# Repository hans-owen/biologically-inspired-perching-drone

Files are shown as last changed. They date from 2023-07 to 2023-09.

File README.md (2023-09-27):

# Biologically Inspired Perching Drone
This project aims to develop an effective attachable modular device for enabling drones to perch on cyclindrical objects, while maintaining the ability to land on flat surfaces. It was originally inspired by the claws of birds of prey and their unique biological ratcheting mechanism that allows them to tightly and securely grip with their talons without relying entirely on muscular strength.

By using 3D printing manufacturing and easy to find off-the-shelf parts we hope to provide a design that is accessible and easily implemented into different drones. Additionally, we hope to make it easy for others to contribute their ideas, modifications, and remixes of original designs.

Currently, only a single preliminary version has been released, which offers effective perching for 5-inch drones that can be manually triggered by a pilot via BetaFlight firmware. Although this is a good first-step/proof-of-concept, the idea has far more potential. Further iterations could offer support to more drones of different sizes and software that functions together with autopilot firmware (e.g., Ardupilot) would allow for full automation.

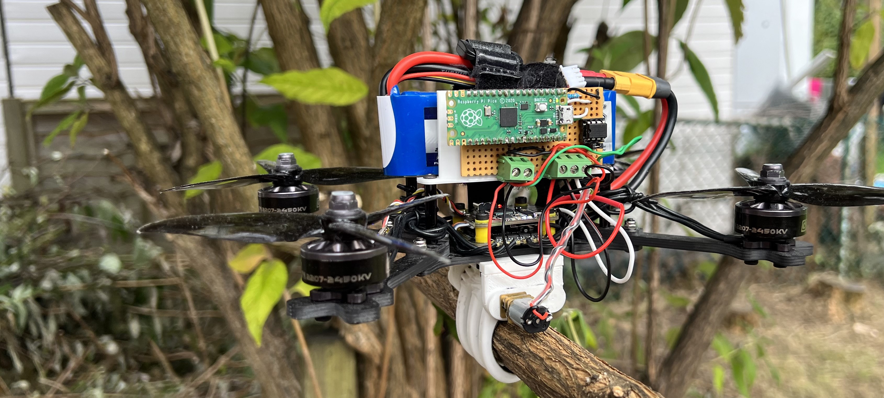
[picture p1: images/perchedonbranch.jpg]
PerchedImage


## Table of Contents
1. Directory Structure
2. Getting Started
   1. 3D Printing
   2. Hardware Assembly
   3. Electronics Assembly
   4. Software
4. How to Use
   1. Setting Up FC firmware
   2. Connect ELRS controller
   3. Actuate Switch
6. Credits
7. Licences

The files within the project contain both the hardware and software required to build a claw attachment for a drone.

## Directory Structure
* [control_code/](./biologically-inspired-perching-drone/claw_control)  - folder containing pico firmware
  * [include/](./biologically-inspired-perching-drone/claw_control/include)
  * [lib/](./biologically-inspired-perching-drone/claw_control/lib)
  * [src/](./biologically-inspired-perching-drone/claw_control/src)
  * [test/](./biologically-inspired-perching-drone/claw_control/test)
  * [platformio.ini](./biologically-inspired-perching-drone/claw_control/platformio.ini)
* [hardware/](./biologically-inspired-perching-drone/hardware)          - folder containing hardware (both electronics & CAD)
* [README.md](./biologically-inspired-perching-drone/README.md)

## Getting Started
To get started with constructing the modular perching attachment for drones ensure you have the following components, links (UK purchasers) have been provided to the exact components used in our version of the build:
#### Claw
* [3D Printer](https://www.crealityofficial.co.uk/products/official-creality-ender-3-3d-printer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)
* [PLA Filament](https://www.amazon.co.uk/s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)
* [4x OD12mm, ID8mm Bearings](https://simplybearings.co.uk/shop/p2772/Budget-MR1282Z-Metal-Shielded-Deep-Groove-Ball-Bearing-8x12x3.5mm/product_info.html)
* [4x 25mm M3 Screws](https://www.accu.co.uk/cap-head-screws/2804-SSC-M3-25-A2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)
* [2x M1.5 Self-tapping Screws](https://cpc.farnell.com/neutrik/a-screw-1-8/screws-for-d-mounts-a-type/dp/AV18050?mckv=s_dc|pcrid|426684131039|kword||match||plid||slid||product|AV18050|pgrid|100371158878|ptaid|pla-1869734976461|&CMP=KNC-GUK-CPC-SHOPPING-9262013734-100371158878-AV18050&s_kwcid=AL!5616!3!426684131039!!!network}!1869734976461!&gclid=CjwKCAjwivemBhBhEiwAJxNWN8YT4Eb2GvifQI9ZS6wh_OzB7m4AdSvY-hiyPY48TIBvsaB6Vbc0dBoCt_0QAvD_BwE)
* [Sand Paper 120 Grit (lower grit works better)](https://www.amazon.co.uk/s?k=sandpaper&crid=HUOTKIT8XZ5P&sprefix=sandpap%2Caps%2C128&ref=nb_sb_noss_2)
* [Super Glue](https://www.amazon.co.uk/Gorilla-4044205-Superglue-15g/dp/B003CT4XT0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)
* [Raspberry Pi Pico](https://thepihut.com/products/raspberry-pi-pico)
* [Metal-Geared DC Motor 298:1](https://thepihut.com/products/micro-metal-gearmotor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)
* [22AWG Black, Red, and White Wire](https://www.amazon.co.uk/TUOFENG-Electric-Flexible-Different-Electronic/dp/B07G72DRKC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)
* [L9110H H-Bridge](https://thepihut.com/products/l9110h-h-bridge-motor-driver-for-dc-motors-8-dip?variant=39823794634947)
* [10Ω Resistor](https://thepihut.com/products/resistor-packs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)
* [Strip Board](https://thepihut.com/products/universal-proto-board-pcbs-4cm-x-6cm-3-pack)

#### Drone
Here is a list of the components we used in the construction of test drone in case you would like directly replicate the build, however this project can be easily adapted to any drone flight controller:
* [SpeedyBee F405V3 Flight Controller + ESC Stack](https://www.unmannedtechshop.co.uk/product/speedybee-f405-v3-bls-50a-4in1-flight-stack/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)
* [Motors](https://cheapdrone.co.uk/dys-sun-fun-sf2207-2207-2400kv-2750kv-4-5s-brushless-motor-cw-thread-for-rc-drone-fpv-racing-drone-parts)
* [BetaFlight ELRS Reciever](https://www.unmannedtechshop.co.uk/product/betafpv-elrs-lite-receiver-2-4ghz-flat-antenna/)
* [TBS Open Source Drone Frame](https://www.quadcopters.co.uk/tbs-source-one/tbs-source-two-racing-frame-v01)
* [LiPo](https://www.amazon.co.uk/GOLDBAT-Battery-Airplane-Quadcopter-Helicopter/dp/B0BVZDYGQ8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)

### 3D Printing
To 3D print the mechanicals parts for the perching claw, you need to download the relevant STL files from the link below:

When printing components with gears ensure that the layers of the print are parallel to the direction of force transmission from the gear to reduce the risk of gears shearing (see below). The design is fully finctional with 100% in-fill PLA, however, can be made more robust using PETG or ABS filaments.

If you wish to remix the hardware designs, the SolidPart files can also be found from the link above and consider submitting the modified design as a remix so that others can easily find custom designs that may be useful for them.

### Hardware Assembly
1. After printing cut out and attach sandpaper to the inside of the claw with superglue to provide a high friction surface for the gripper.
2. Attach the metal-geared DC motor to the side mount of your choice and screw in place with the 1.5mm self tapping screws.
3. After the motor is attached, press-fit the bearings into each of the cut-outs in the side mounts.
4. Press fit the claw onto the motor and bearings, ensure that when the two claw part gears mesh that the claws themselves are parallel with each other.
5. Press fit M3 nuts into the cut-outs on the top mount.
6. Attach and super-glue the top mount to the side mounts with claws attached by inserting the side mount tabs into the top mount.
7. Attach the gripper to the drone by threading the 25mm M3 screws through the flight controller mount and the drone frame, screw them into the nuts of 3D-printed top mount until the FC and the gripper are firmly attached to the drone frame. (Do not overtighten as this can cause damage to your FC!)

This concludes the hardware assembly of this project, next we move onto the electronics and finally conclude with the software.

### Electronics Assembly
We recommend to first layout the circuit on a breadboard (see picture below) and perform a test to ensure all your components are functional before soldering them to a prototyping board.
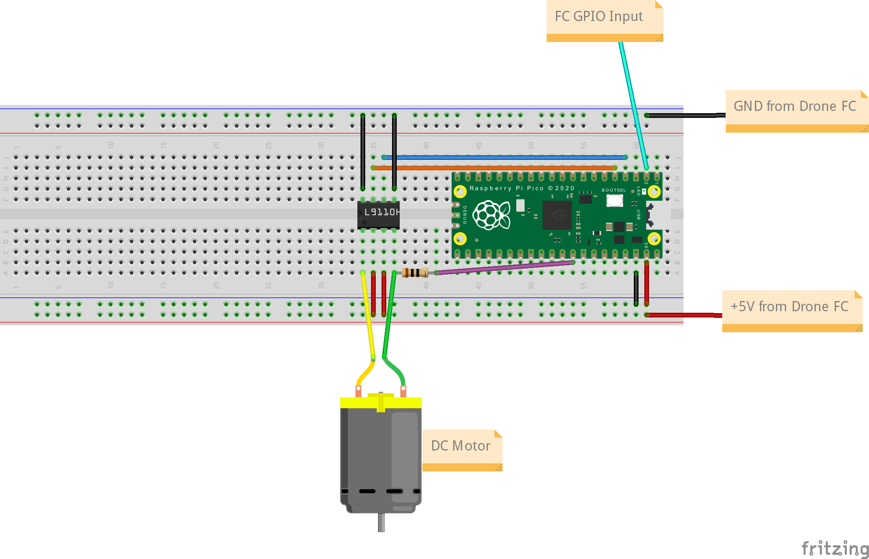
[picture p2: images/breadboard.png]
Breadboard/


The simple circuit uses a Raspberry Pi Pico to take a 3.3V GPIO output from the drone FC and use it to actuate the claw mechanism via an H-bridge. This FC GPIO pin can be mapped to the RF transmitter to manually actuate the claw or be addressed directly in the FC firmware. A shunt resistor is used to measure the current used by the motor and turn off the motor when the claw is fully opened to prevent the mechanism from damaging itself and wasting power. Once the circuit is functional on a breadboard it can easily be soldered together using strip-board for a permanent solution capable of being mounted on the drone.
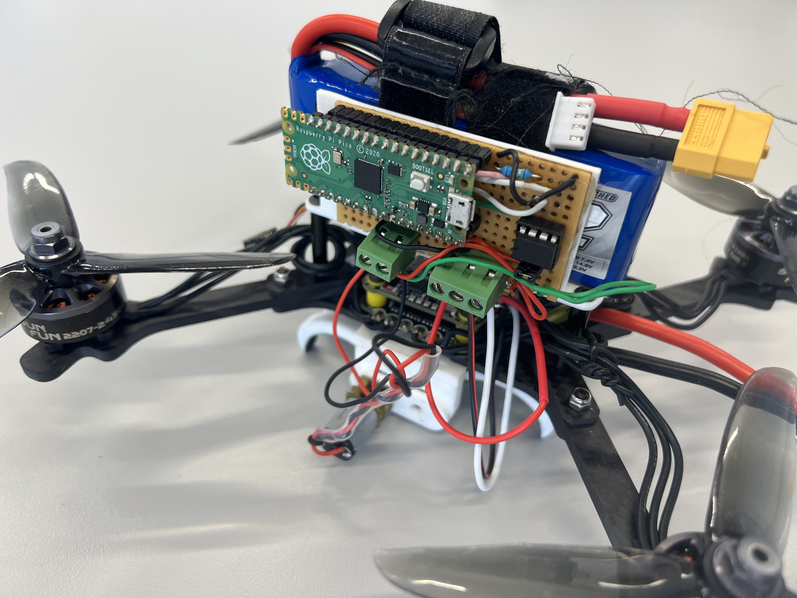
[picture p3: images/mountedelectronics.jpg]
ElectronicsMount/


### Software

The software was developed using VS Code and platform.io to compile the code for the Raspberry Pi Pico using the Arduino framework. To compile the firmware for yourself, download the control_code directory and open in VS Code with the platform.io plug-in, once the project is recognised simply compile the code using platform.io and upload the firmware.uf2 file to the RPi Pico via the boot button. To set up the drone FC firmware see how to use section below.

## How to Use

Once the hardware and electronics have been assembled and the mechanism software has been uploaded, to function the mechanism expects a GPIO output from the FC to actuate the claw. This tutorial focuses on manual actuation of the claw via an RF transmitter used to fly the drone manually, specifically using BetaFlight firmware.

### Setting Up FC Firmware
BetaFlight is the most common drone FC firmware for FPV drones and offers a stable platform for quickly enabling the manual flight of a custom built drone.
1. First set up BetaFlight according to the specifications of your FC of choice and drone set up (link to [General BetaFlight Tutorial](https://www.youtube.com/watch?v=udOHBCORSrE)).
2. To enable a GPIO pin on the FC for the claw mechanism GPIO resource remapping is required, here we have embedded a good YT tutorial with resources that show how to easily implement this with your drone set up. [BetaFlight Resource Remapping Tutorial](https://www.youtube.com/watch?v=-DiGLYbl1Jk).
3. Ensure that the GPIO pad you select on the FC has a wire connecting it to the correct pin on the RPi Pico, along with VCC and GND for powering the Pico.

Another common FC firmware is iNav, which offers some automation advantages over BetaFlight by including automated drone pathing, auto-hover, return-home, etc.
1. Set up iNav according to the specification on your FC and drone set up (link to [General iNav Tutorial](https://www.youtube.com/watch?v=TXAzmrhjKNI)).
2. To perform resource remapping on iNav is more difficult than in BetaFlight, to do this you have to download the [iNav source code](https://github.com/iNavFlight/inav) (relevant version!!), modify the resources in the code and then recompile the firmware and manually upload the firmware to the FC (link to [tutorial](https://www.wizzx.tech/552/)).

### Connecting ELRS Controller
Once the GPIO resource has been effectively remapped according to the firmware type and tutorials above, the controller can be bound to actuate this GPIO pad in the firmware configuration (both BetaFlight and iNav). To do this most often the GPIO resource is mapped to USER1, a custom user selectable mode, when setting up RF transmitter. By setting a switch (AUX1,2,3,4 etc.) on the controller to trigger USER1, it triggers the mechanical claw activation. Reflash firmware after ensuring the controller activates USER1.

### Actuate Switch
Finally, when ready to test, unplug the drone from the firmware configurator and ensure LiPo is plugged in and controller is connected. The claw acutation should now be possible when you activate the switch (AUX1,2,3,4 etc.) on your controller that you mapped to your custom user mode (USER1), which pulls the remapped GPIO pin high for the RPi Pico.

## Credits
[MGCorbin](https://github.com/MGCorbin)
[christiankuhlmann](https://github.com/christiankuhlmann)
[T-Omole](https://github.com/T-Omole)
[hans-owen](https://github.com/hans-owen)

## Licenses
Hardware (all files stored under the [hardware](./biologically-inspired-perching-drone/hardware) folder) are under the Creative Commons Attribution-ShareAlike 4.0 International license.

Firmware (all files stored under the [claw_control](./biologically-inspired-perching-drone/claw_control) folder) are under the MIT license.

See each folders LICENSE.txt file for details.

## Hardware
In this folder you can find STL files that can be downloaded for 3D printing and the original parameterised SolidWorks CAD files and assemblies that can be modified to customise/remix the design to suit different drone and hardware configurations. 
* [Bivalve_7_talon/](./biologically-inspired-perching-drone/hardware/Bivalve_7_talon) - folder containing the Solidworks part files and STL files for a version of the bivalve claw mechanism with additional claws (3-4 config).
* [Bivalve_Claw_Mechanism/](./biologically-inspired-perching-drone/hardware/Bivalve_Claw_Mechanism) - folder containing the SolidWorks part files, STL files, and assembly for the bivalve claw mechanism design.
* [Tendon_Arm/](./biologically-inspired-perching-drone/hardware/Tendon_Arm) - folder contianing the STL files used during the testing and development of the tendon claw design.

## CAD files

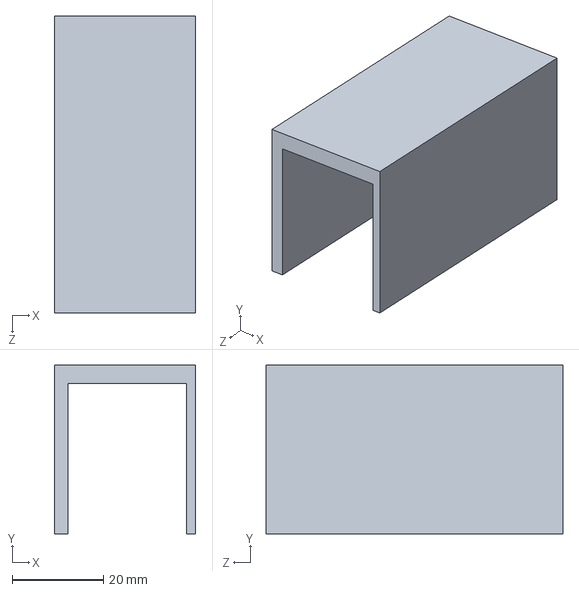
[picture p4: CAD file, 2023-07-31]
hardware/ElectronicsMount.SLDPRT
31.0 x 37.0 x 65.2 mm

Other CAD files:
hardware/ElectronicsMount.STL

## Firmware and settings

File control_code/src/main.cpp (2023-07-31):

#include <Arduino.h>

#define LED_PIN 25
#define FC_SIGNAL_PIN 1
#define MOTOR_FORWARD 2
#define MOTOR_REVERSE 3
#define ADC_PIN 27

int speed = 255;
int currentThreshold = 40;
bool closed = false;

// put function declarations here:
void motorforward() {
  analogWrite(MOTOR_FORWARD, speed);
  analogWrite(MOTOR_REVERSE, 0);
}

void motorreverse() {
  analogWrite(MOTOR_FORWARD, 0);
  analogWrite(MOTOR_REVERSE, speed);
}

void motorstop() {
  analogWrite(MOTOR_FORWARD, 0);
  analogWrite(MOTOR_REVERSE, 0);
}

void showmecurrent() {
  int current = analogRead(ADC_PIN);
  Serial.print("\ncurrent: ");
  Serial.print(current);
  delay(1000);
}

void setup() {
  // put your setup code here, to run once:
  pinMode(LED_PIN, OUTPUT);
  pinMode(FC_SIGNAL_PIN, INPUT);
  pinMode(MOTOR_FORWARD, OUTPUT);
  pinMode(MOTOR_REVERSE, OUTPUT);
  pinMode(ADC_PIN, INPUT);

  Serial.begin(115200);
  Serial.println("Startup...");
}

void loop() {
  // put your main code here, to run repeatedly:
  // Signals
  int current = analogRead(ADC_PIN); // read the current value from the ADC
  int fcSignal = digitalRead(FC_SIGNAL_PIN); // read the FC signal

  if (fcSignal == HIGH){
    // set FC signal status indicator
    digitalWrite(LED_PIN, HIGH); 
    motorforward();
    showmecurrent();
  }
  3
                                                                                                                                                                                      
  else if (fcSignal == LOW){
    // set FC signal status indicator
    digitalWrite(LED_PIN, LOW); 
    current = analogRead(ADC_PIN);
    if (current > currentThreshold){
      while (fcSignal == LOW){
        motorstop();
        showmecurrent();
        fcSignal = digitalRead(FC_SIGNAL_PIN);
      }
    }
    else {
      motorreverse();
      showmecurrent();
    }
  }
}

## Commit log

2023-07-31 Update control code.
    [ElectronicsMount.SLDPRT, ElectronicsMount.STL]
2023-07-31 Delete ClawCode2.0 directory
    This code is no longer compatible with the updated electronics hardware.
    [main.cpp]
2023-07-31 Delete claw_control directory
    Removing deprecated code.
2023-08-25 Update README.md
    Added hardware assembly instructions.
2023-08-25 Update README.md
    Begin electronics assembly instructions.
2023-09-27 Mounted electronics image.
